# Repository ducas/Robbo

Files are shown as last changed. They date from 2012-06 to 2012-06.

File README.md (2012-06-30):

# Hello Robbo!

## A .Net Micro Framework Tank Bot

This project aims to build an automated tank bot using the .Net Micro Framework.

## Parts

### Electronics

* FEZ Panda II [Datasheet](https://raw.github.com/ducas/Robbo/master/Datasheets/FEZ_Panda_II_UserManual.pdf)
* Motor Driver 1A Dual TB6612FNG (ROB-09457) [Datasheet](https://raw.github.com/ducas/Robbo/master/Datasheets/TB6612FNG.pdf)
* Triple Axis Accelerometer Breakout - ADXL345 (SEN-09836) [Datasheet](https://raw.github.com/ducas/Robbo/master/Datasheets/ADXL345.pdf)
* Ultrasonic Range Finder - MaxBotix LV-EZ0 (SEN-08502) [Datasheet](https://raw.github.com/ducas/Robbo/master/Datasheets/MB1000_Datasheet.pdf)
* 4xAAA Battery Holder
* 1x9V Battery Holder

### Moving Stuff
* Tamiya Plate Set 70157
* Tamiya Track and Wheel Set 70100
* Tamiya Dual Gearbox 70168
* Low Current Replacement Motors - Solarbotics RM3

## Hooking Things Up

The Fritzing diagram is included in the Fritzing directory (both as a Fritzing file and PNG).

Wiring Diagram

* 4xAAA -> Motor Driver
	* Red -> VM
	* Black -> GND
* 9V -> FEZ Panda
	* Red -> Vin
	* Black -> GND
* Accelerometer -> FEZ Panda
	* SCL -> D3 (SCL)
	* SDA -> D2 (SDA)
	* SDO -> GND
	* CS -> 3.3V
	* VCC -> 3.3V
	* GND -> GND
* Motor Driver -> FEZ Panda
	* PWMA -> D10 (PWM6)
	* AIN0 -> D9
	* AIN1 -> D8
	* STBY -> D7
	* PWMB -> D6 (PWM1)
	* BIN0 -> D5
	* BIN1 -> D4
	* VCC -> 5V
	* AOUT0/1 -> Left Motor
	* BOUT0/1 -> Right Motor
* Distance Sensor -> FEZ Panda
	* GND -> GND
	* +5 -> 5V
	* RX -> D11
	* AN -> A0

## Finally - The Code!

### Devices

* Motor Driver - represented by MotorDriver class which allows for moving forward and reverse along with turning left and right.
* Motor - represented by Motor class which uses PWM and digital ports to provide basic forward, reverse and stop methods.
* Ultrasonic Distance Sensor - represented by UltrasonicDistanceSensor class which uses analog input and control port to provide distances in cm.
* Accelerometer - represented by Accelerometer class which uses I2C to communicated with sensor and calculate gravitational force in 3 axes.
* Piezo - represented by Piezo class which uses PWM to play tones.
* Bumper - represented by Bumper class which uses interrupts to raise an event when the switch is pressed and circuit is closed.

### Bots

This project has several bot implementations. These bots are either simple test bots to test certain components or autonomous bots.

* Test Bots
	* AccelerometerTestBot - Prints acceleration from accelerometer to debug output.
	* BumperTestBot - Listens for Bumped event and prints to the debug output.
	* MotorDriverTestBot - Outputs different speeds and signals to control the channels on the motor driver.
	* MotorTestBot - Drives the motors in forward and reverse patterns.
	* PiezoTestBot - Plays some cute tunes on a Piezo buzzer.
	* UltrasonicDistanceSensorTestBot - Prints distance from the ultrasonic range finder to debug output.
* Autonomous Bots
	* DiscoveryBot - Uses the motor driver and ultrasonic range finder to drive the tank bot around and try not hit things.
	* SafeDiscoveryBot - Uses the motor driver, ultrasonic range finder and accelerometer to drive the tank bot around and try not hit things, but get out of trouble when elevations change.
	* VacuumBot - Uses the motor driver and ultrasonic range finder to drive the tank bot around in circles without running into things.

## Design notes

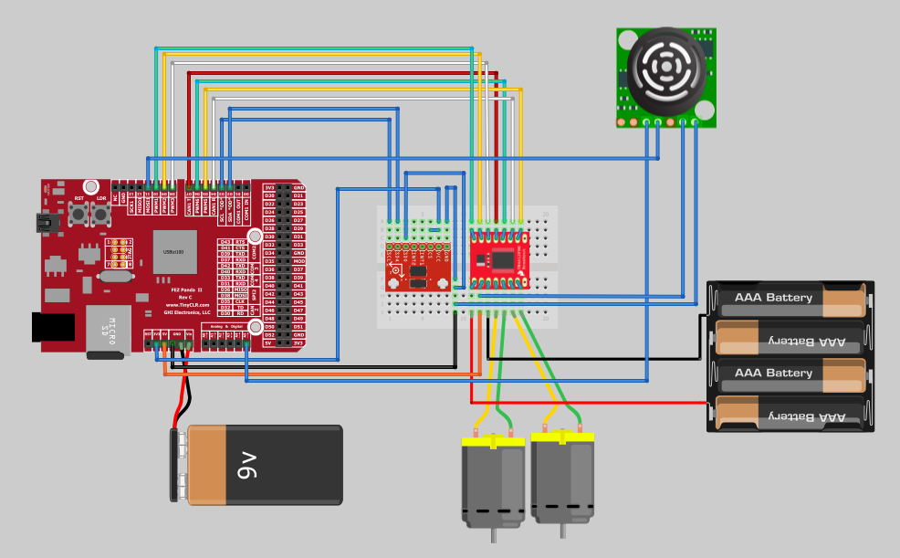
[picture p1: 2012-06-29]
Fritzing/robbo.PNG

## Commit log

2012-05-28 change pwm set 0 to set false
2012-05-28 renamed distance sensor to IR distance sensor and added Ultrasonic distance sensor
2012-05-28 changed robot's front distance sensor to ultrasonic sensor.
2012-06-22 Changed Motor implementation to have forward and reverse ports and removed inversion.
2012-06-22 Added H Bridge Motor Driver Implementation
2012-06-22 Added implementation of motor driver bridge
2012-06-22 renamed motor driver
2012-06-22 added test bots for motors, motor driver and ultrasonic distance sensor
2012-06-22 renamed motor driver class and set test bot to have more realistic sleeps
2012-06-24 Created DeviceInitializer to construct devices with default config.
2012-06-26 moved bots and devices into folders/namespaces
2012-06-26 Added bumper switch implementation with test bot
2012-06-27 Added accelerometer implementation and safe discovery bot that (hopefully) doesn't flip.
2012-06-28 made safe discovery bot react to accelerometer values by moving away from elevated end
2012-06-29 added fritzing schematic and image
    [robbo.fzz]
2012-06-29 fixing SD pin names on accelerometer mapping
2012-06-29 added pin assignments for motor driver
2012-06-29 fixed switch of accel and range datasheet links
2012-06-30 added devices and bots to readme.
